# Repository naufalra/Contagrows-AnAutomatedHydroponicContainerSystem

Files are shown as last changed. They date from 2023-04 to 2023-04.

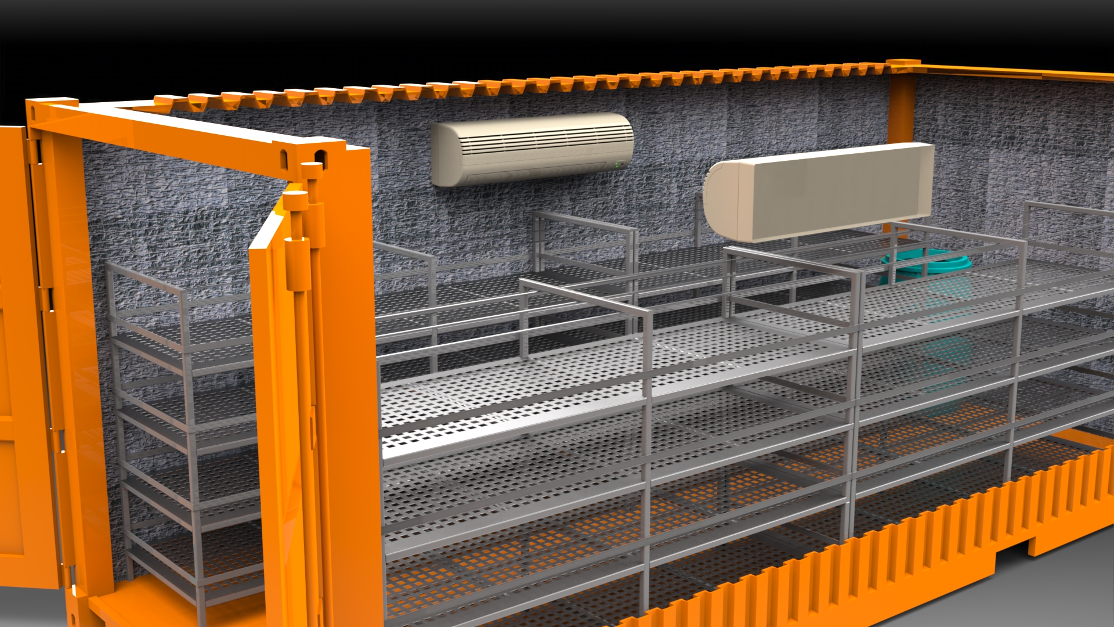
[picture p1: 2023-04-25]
3. Mechanical/render 2.jpg

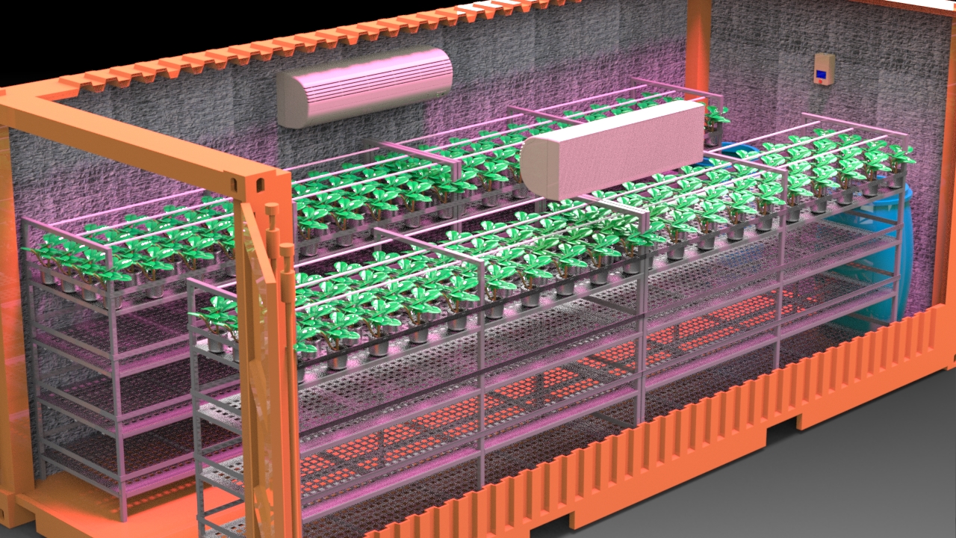
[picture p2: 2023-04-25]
3. Mechanical/Contagrov 3.jpg

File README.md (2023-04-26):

# Contagrows - An Automated Hydroponic Container System
# Project Overview

Container farms are becoming increasingly popular within the controlled environment agriculture industry. These farms are usually vertical farming systems installed inside a shipping container. The main objective is to make sure the local temperature is below 16 degrees Celcius with 80% of humidity so the plant can grow inside a controlled hygiene container. To do so, the container is equipped with AC, Fans, and an automatic watering and monitoring system.



During the manufacturing process, we had a lot of discussions with good friends from agricultural technology and PIAT (Center for Agro-Technology Innovation) UGM to produce a suitable and sustainable product.

Among our discussion topics was the system's design to meet the plant and electronic requirements. The discussion process resulted in the flow chart below



# Directory

To short things out, this is the directories of this project.

- [Article](https://www.linkedin.com/posts/naufalaryaputra_contagrow-an-automated-container-hydroponic-activity-6986608747372494849-8hf9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)
 - [Electrical Design](https://github.com/naufalra/Contagrows/tree/main/1.%20Electrical)
 - [Mechanical Design](https://github.com/naufalra/Contagrows/tree/main/3.%20Mechanical)
 - [Arduino Program](https://github.com/naufalra/Contagrows/tree/main/2.%20Firmware)

# Intelligent property rights

**Alat Otomasi dan Monitoring Budidaya Hidroponik**

```bash
  https://pdki-indonesia.dgip.go.id/detail/A00202203526?type=di&keyword=A00202203526 
```

**Media Tanam Pertanian Vertikal Hidroponik pada Kontainer**

```bash
 https://pdki-indonesia.dgip.go.id/detail/A00202203525?type=di&keyword=A00202203525
```

# Final Result
Electrical

## Electronics System
The control system itself is using Arduino Mega2560 as the main processor. The Arduino is connected to several built in sensors like DHT11, BME280, the boards is also provide more ports for additional sensor.
Electrical

## Wiring
We divided the panel into two parts to simplify the troubleshooting process and panel tidiness. 

The right panel (the one without LCD) functions as an electrical panel directly connected to the source. This panel also acts as the main switch.

The second panel only serves as the system control and automation of the tool. All control, monitoring, and automation are done through this panel. It is on this panel that the Arduino and sensors are placed.
Electrical

Electrical

We realize that many things can be improved in our electronic and wiring systems, but we have not had the chance to do so due to limited time. The safety process has also not been maximized because all energy has been diverted to the automation system.

## Mechanical Design
This system utilizes a 20-foot container to work. The container was chosen because it is easier to place in urban areas. Still, on the inside, we added several other components to support the needs, including plant shelves, setting panels, and screen protectors on boards to protect from water and dust.

### Shelf
The shelf is designed to accommodate approximately 1000 plant seeds placed in polybags. The rack design considers the plant seeds' maximum capacity and the container's space.

Shelfs

### Panel Box
The panel box is used as the setting center of the tool before the automation process takes place. In addition, on the panel, there is also a sensor reading value viewer to be monitored.

PanelBox

### LCD protectors
We also ad LCD protector as an additional protection for LCD from dust and water drops.
PanelBox

## Overall System
This is the final result of recent design
PanelBox

PanelBox

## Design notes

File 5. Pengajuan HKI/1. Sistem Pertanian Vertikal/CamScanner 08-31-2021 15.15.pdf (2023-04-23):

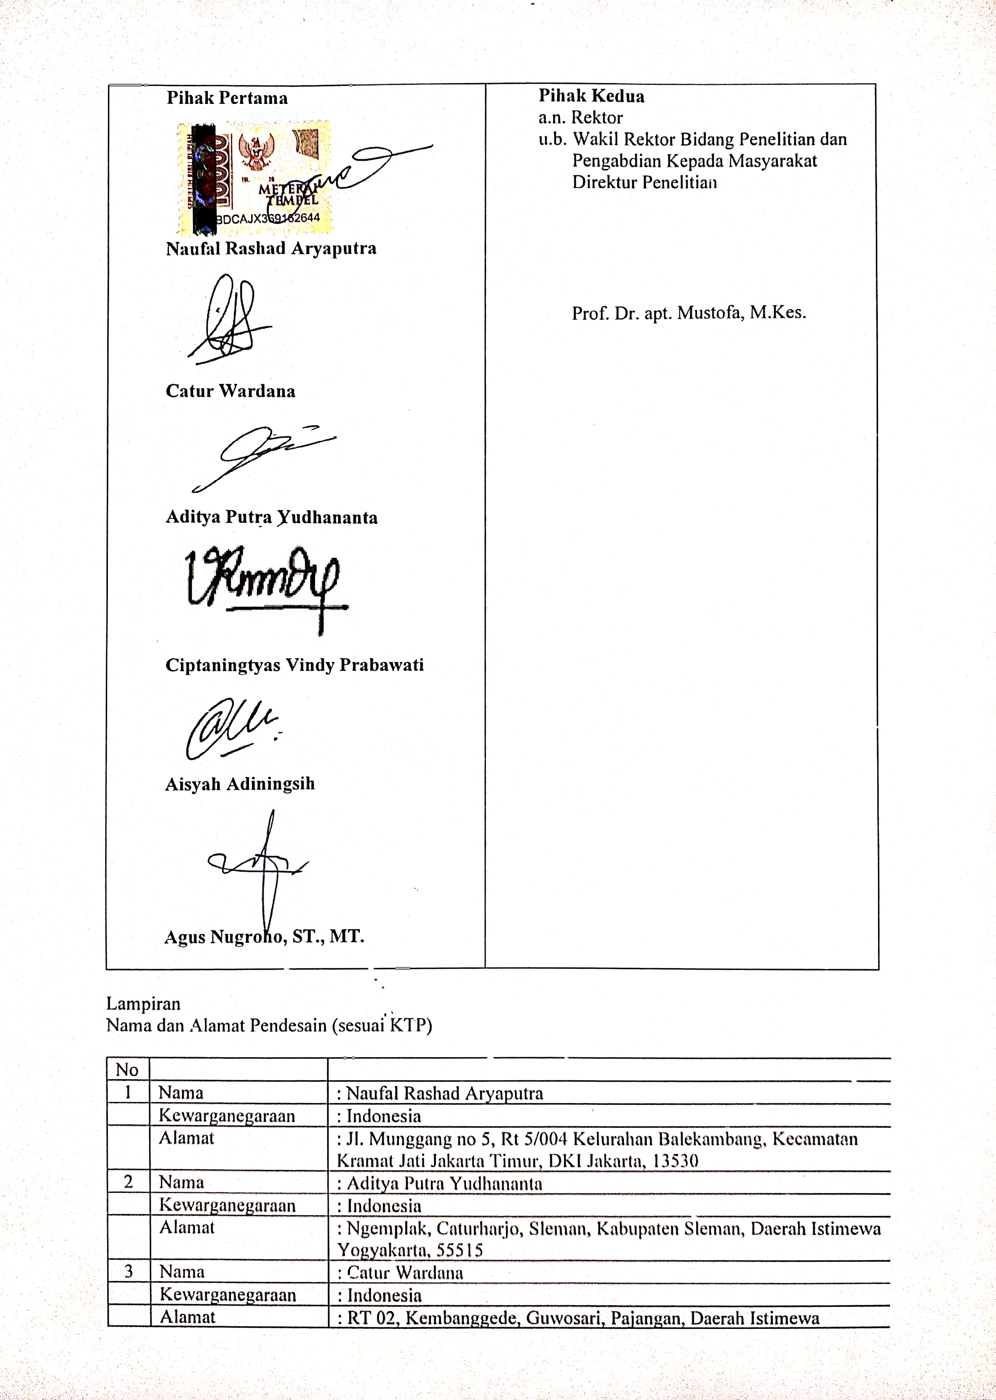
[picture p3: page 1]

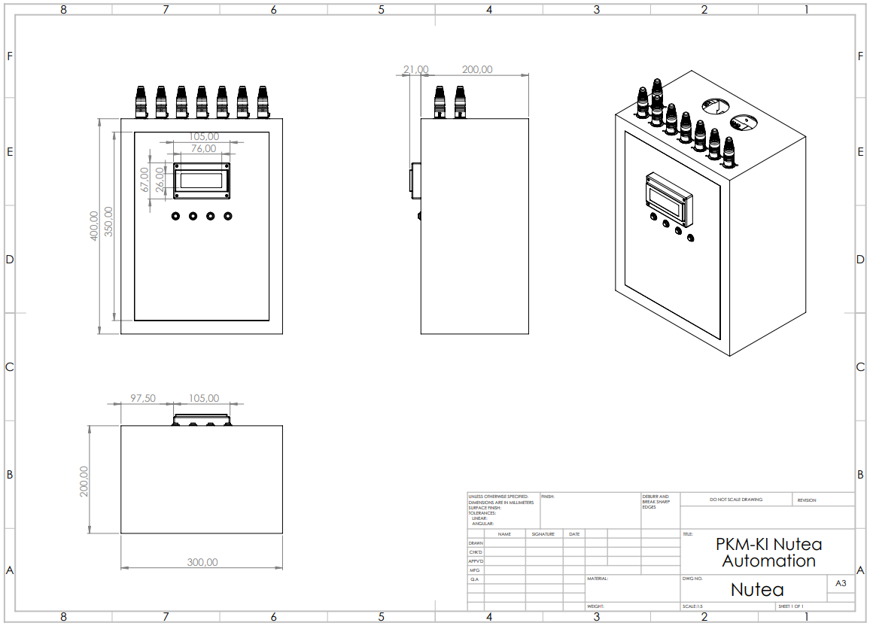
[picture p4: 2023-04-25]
3. Mechanical/Panel.png

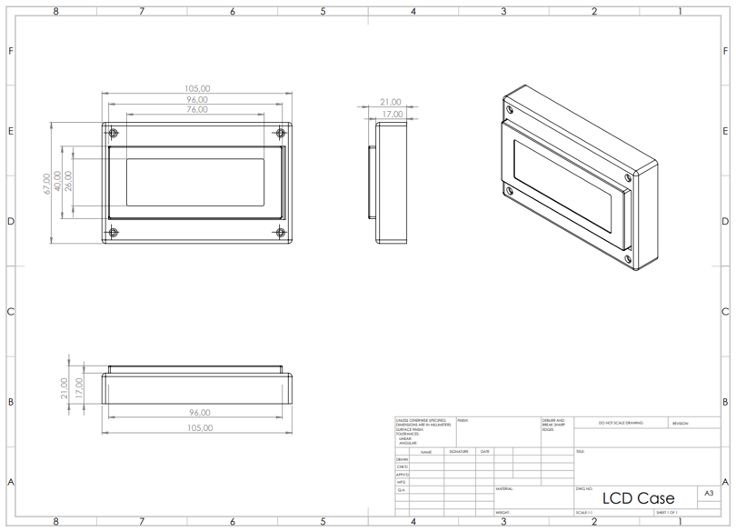
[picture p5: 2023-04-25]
3. Mechanical/LCD.png

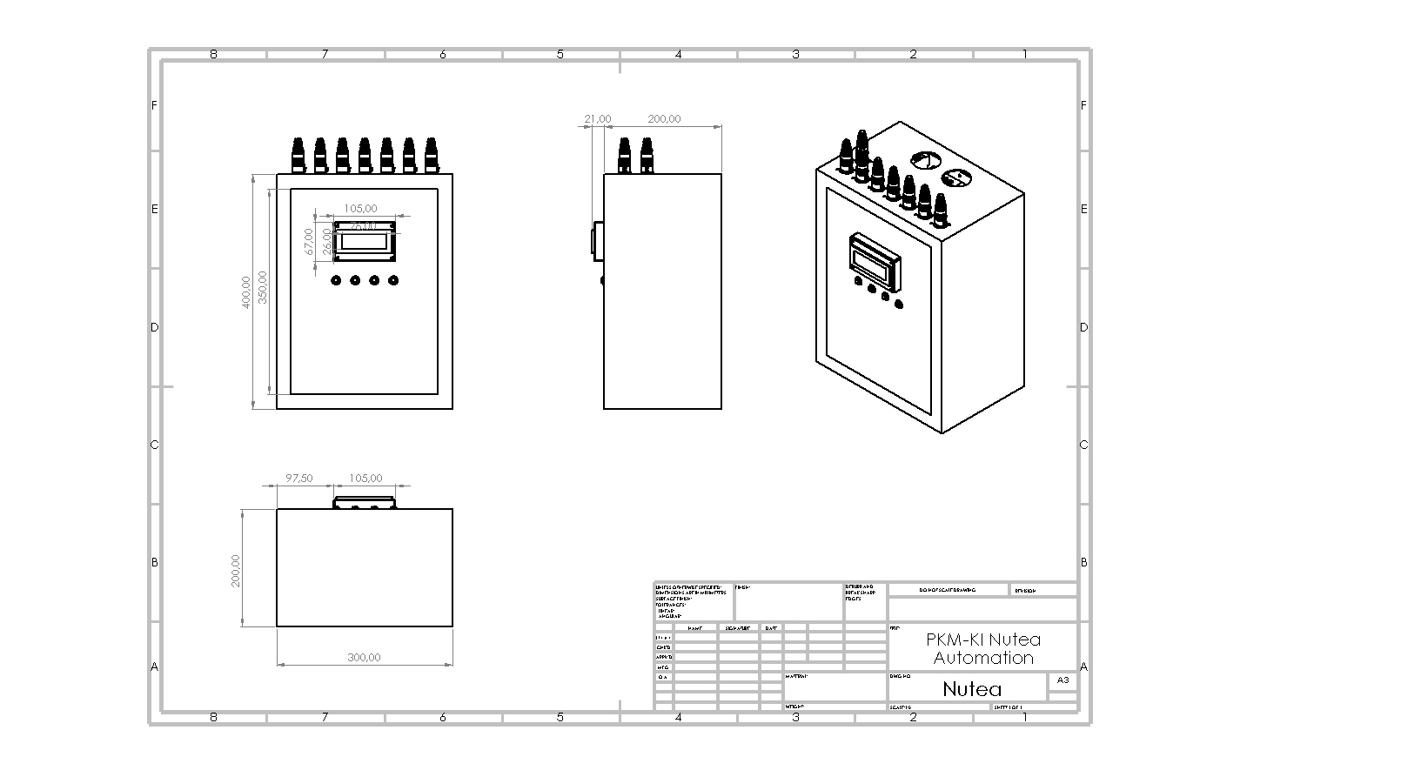
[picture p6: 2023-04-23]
3. Mechanical/Kotak Panel/Kotak Panel.JPG

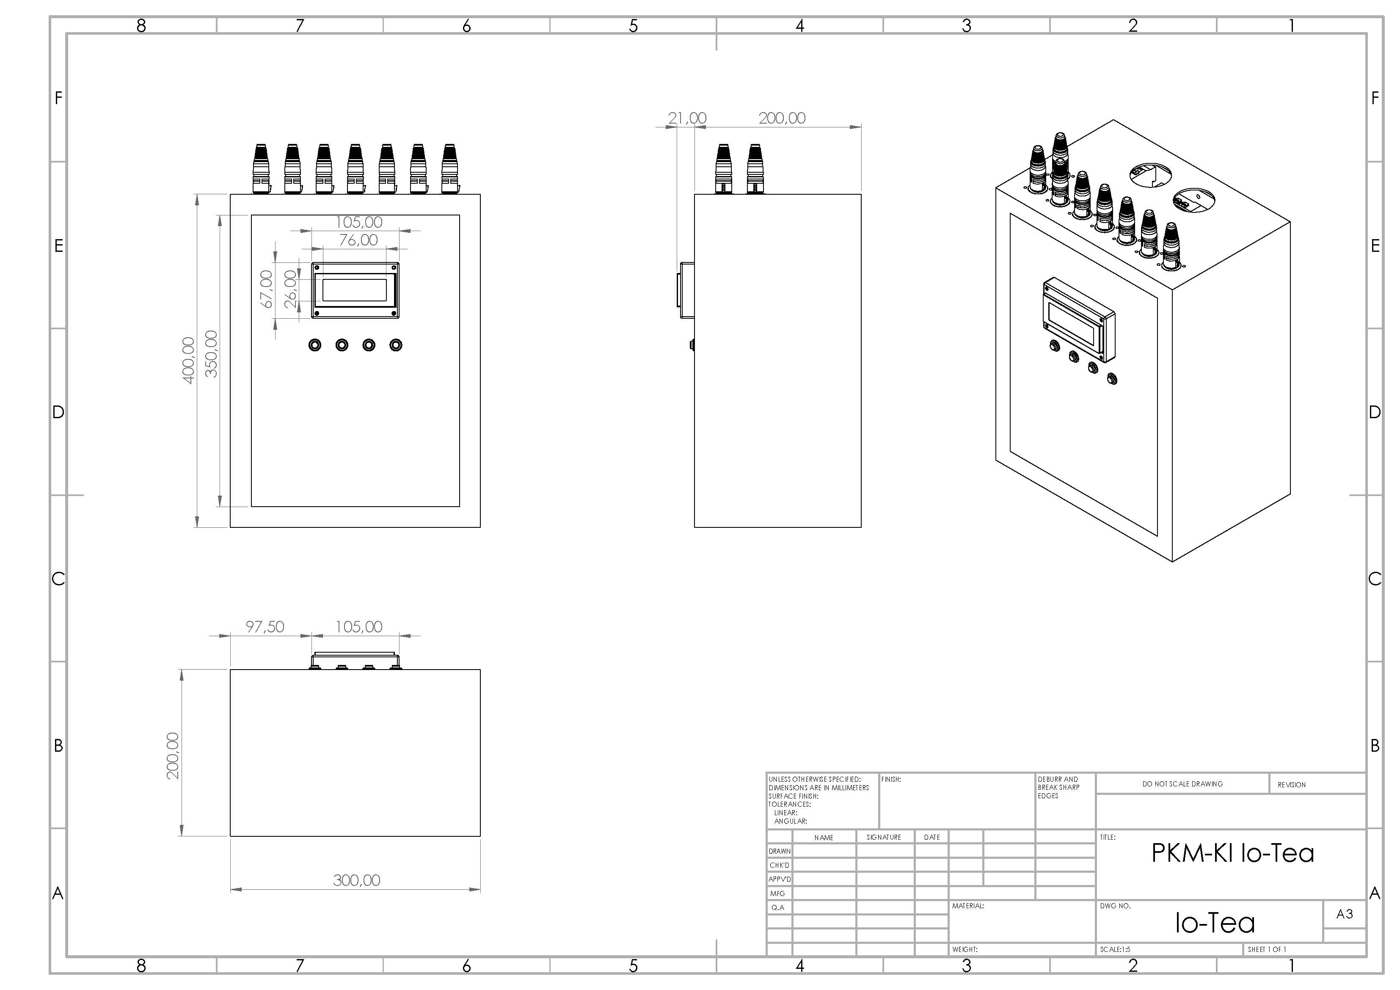
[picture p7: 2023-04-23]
3. Mechanical/Kotak Panel/LALALALLA.jpg

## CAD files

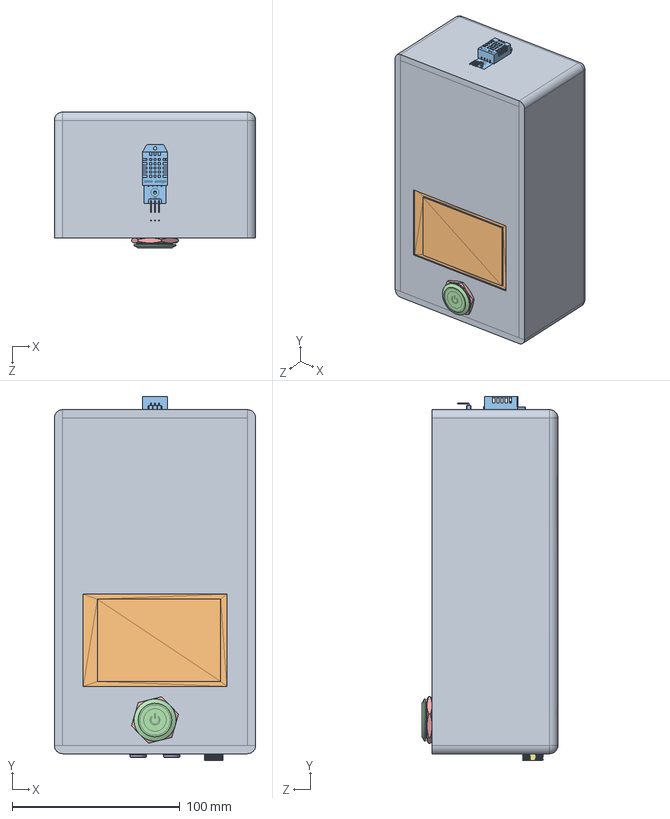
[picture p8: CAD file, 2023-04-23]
3. Mechanical/Shipping Container Assembly/Box.SLDASM
120.0 x 216.8 x 81.0 mm
NX4832T035
DHT22
22mm按钮
22mm金属按钮螺母
Amphenol RF 122440.step x 2
DC jack external.step

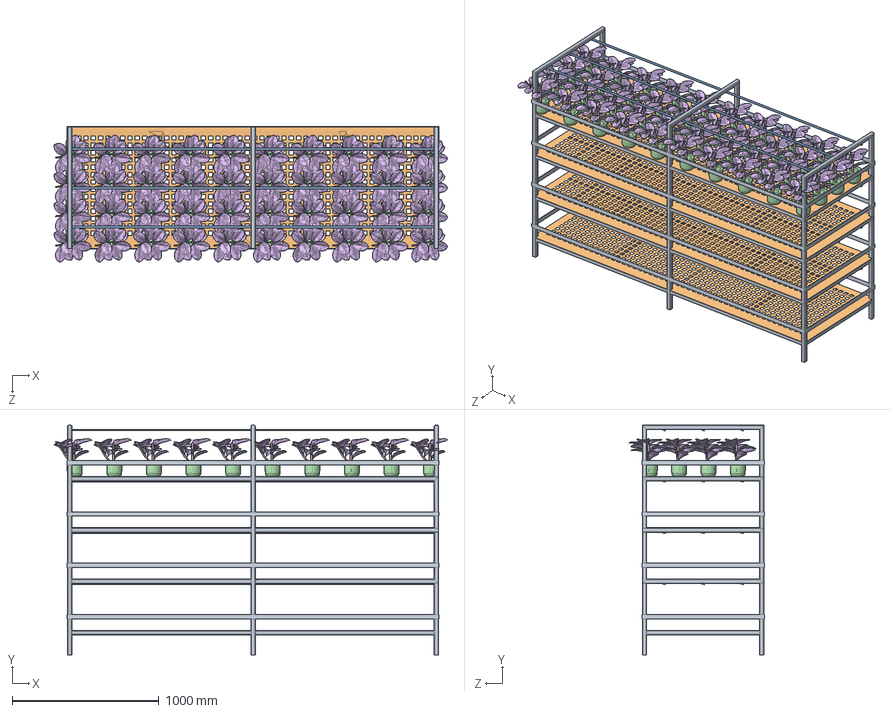
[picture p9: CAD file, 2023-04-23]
3. Mechanical/Shipping Container Assembly/Rak Assy Independ.SLDASM
2686.7 x 1565.0 x 926.4 mm
rak 1
plat x 4
LED SLOT x 4
B23-Vazo x 40
B23-Dal 1 x 40
B23-Yaprak 1 x 400

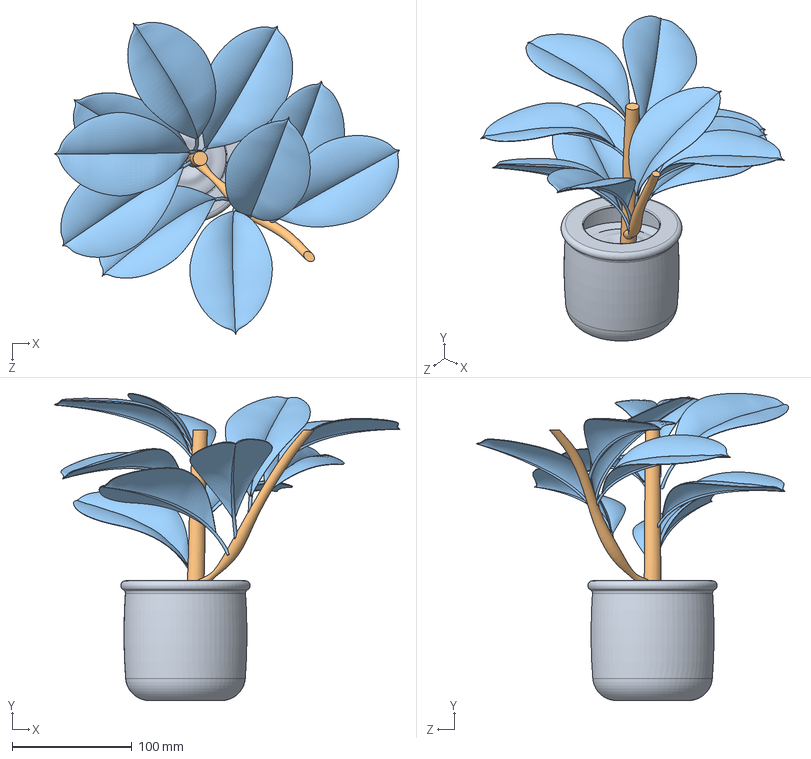
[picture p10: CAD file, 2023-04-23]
3. Mechanical/Shipping Container Assembly/B23-Montaj.SLDASM
288.7 x 256.3 x 260.6 mm
B23-Vazo
B23-Dal 1
B23-Yaprak 1 x 10

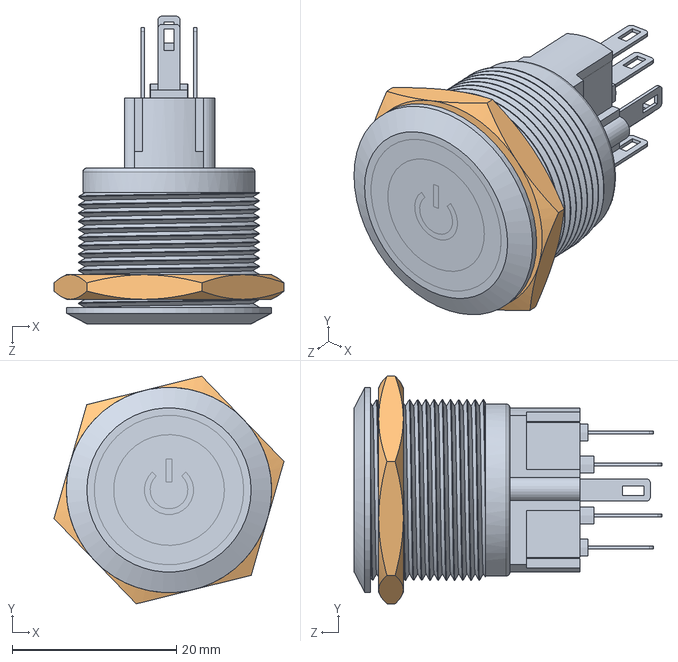
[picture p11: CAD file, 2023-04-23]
3. Mechanical/Shipping Container Assembly/22mm不锈钢按钮.SLDASM
28.0 x 27.7 x 37.5 mm
22mm按钮
22mm金属按钮螺母

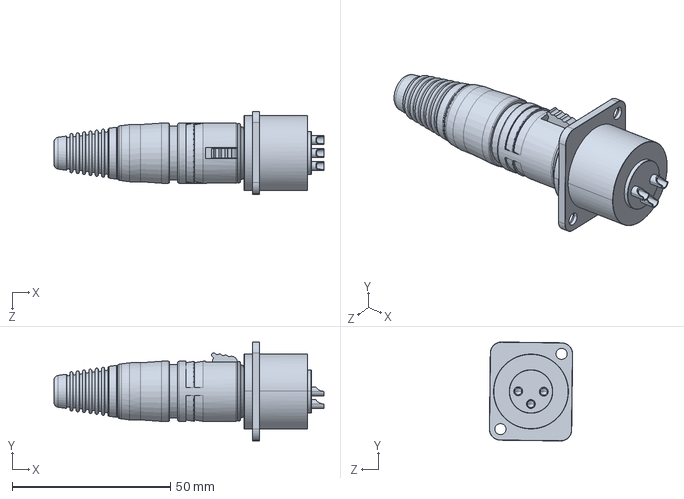
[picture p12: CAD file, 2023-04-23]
3. Mechanical/Kotak Panel/Assem2.SLDPRT
85.2 x 31.2 x 26.3 mm

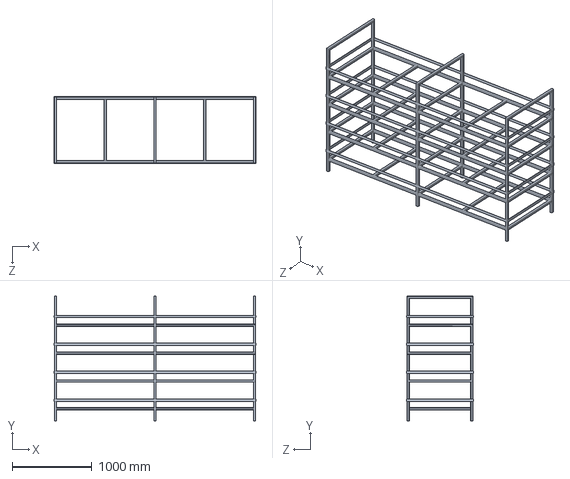
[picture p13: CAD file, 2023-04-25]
3. Mechanical/Rak/Rak_Contagrow.SLDPRT
2538.0 x 1565.0 x 836.0 mm

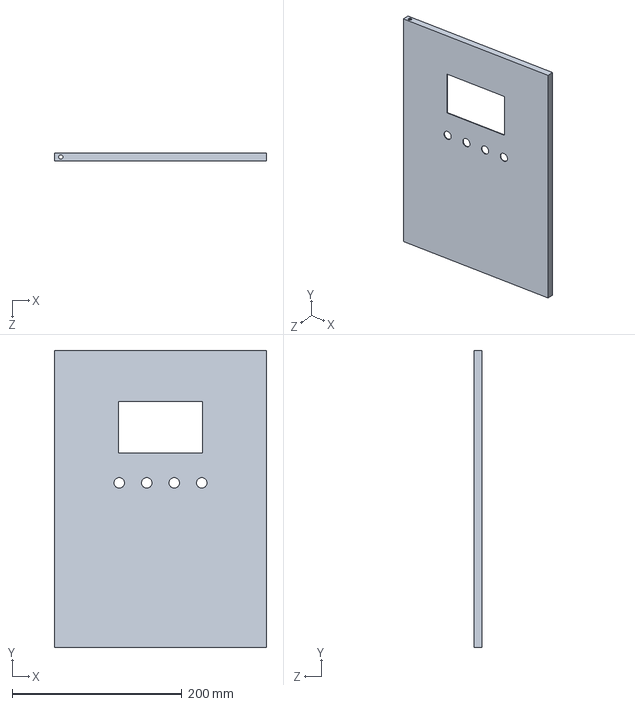
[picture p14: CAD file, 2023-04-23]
3. Mechanical/Kotak Panel/Kotak Panel_2.SLDPRT
250.0 x 350.0 x 10.0 mm

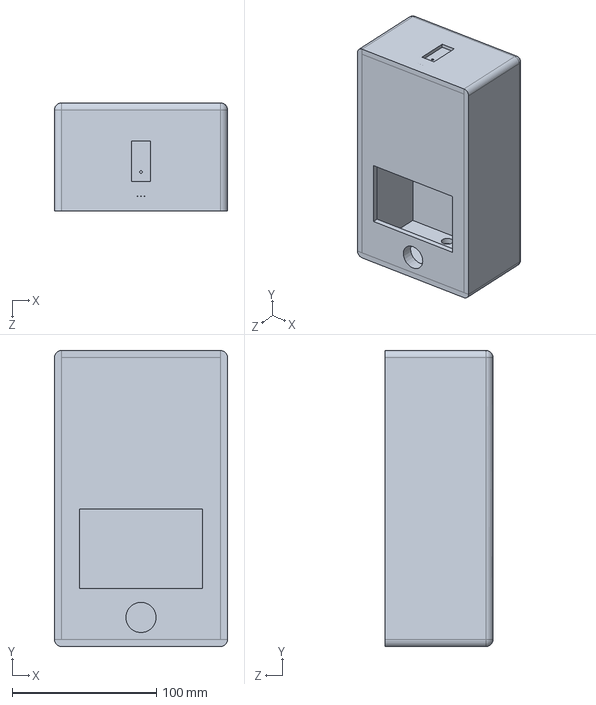
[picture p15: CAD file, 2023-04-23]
3. Mechanical/Shipping Container Assembly/Part2.SLDPRT
120.0 x 205.0 x 75.0 mm

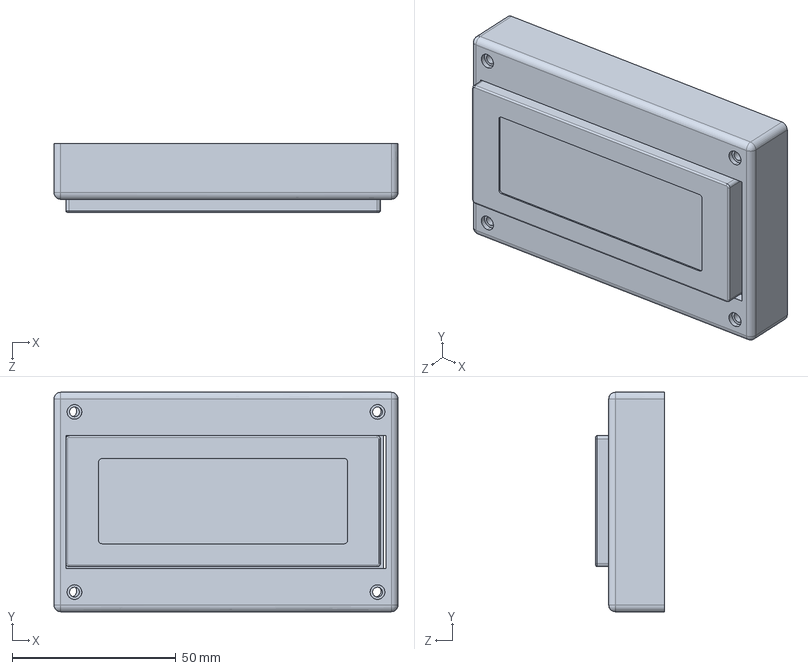
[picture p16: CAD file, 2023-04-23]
3. Mechanical/Kotak Panel/LCD.SLDPRT
105.0 x 67.0 x 21.0 mm

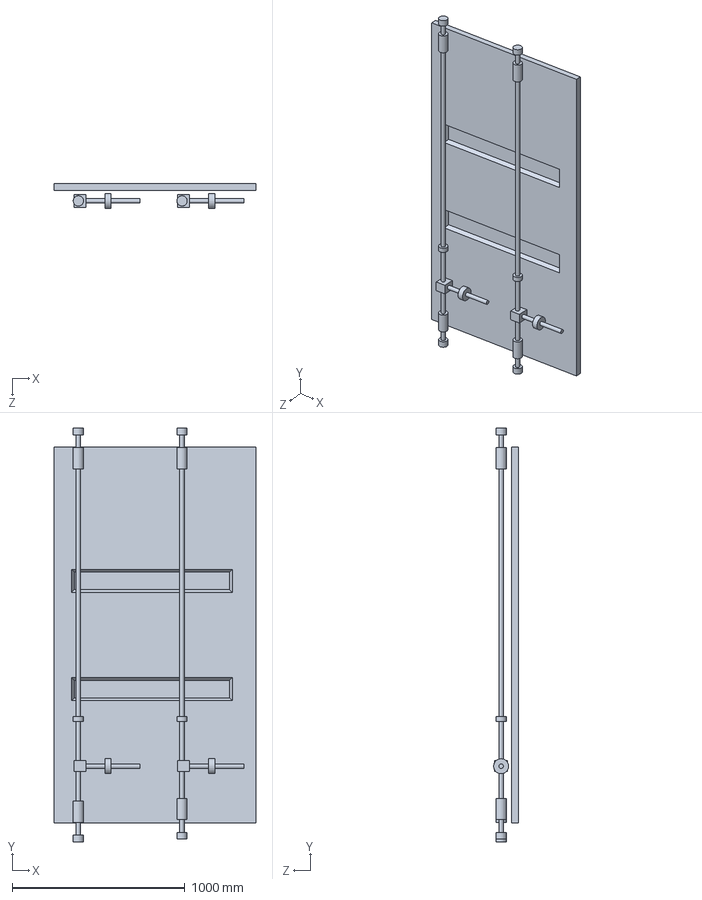
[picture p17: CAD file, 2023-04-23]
3. Mechanical/Shipping Container Assembly/Shipping container door.SLDPRT
1167.0 x 2396.0 x 143.5 mm

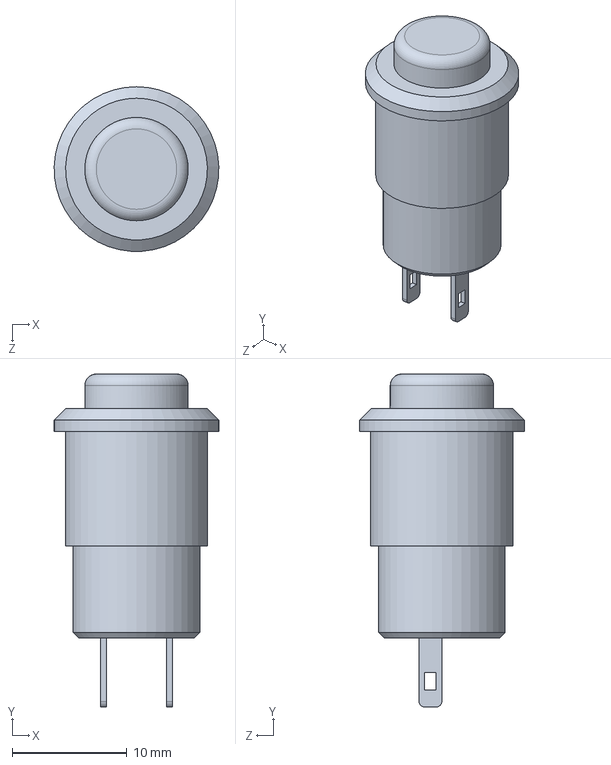
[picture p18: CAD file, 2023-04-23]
3. Mechanical/Kotak Panel/Push Button.SLDPRT
14.3 x 29.0 x 14.3 mm

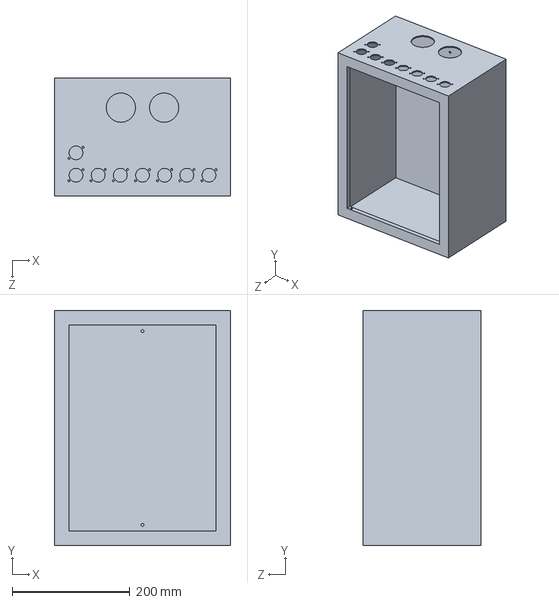
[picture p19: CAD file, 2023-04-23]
3. Mechanical/Kotak Panel/Kotak Panel_1.SLDPRT
300.0 x 400.0 x 200.0 mm

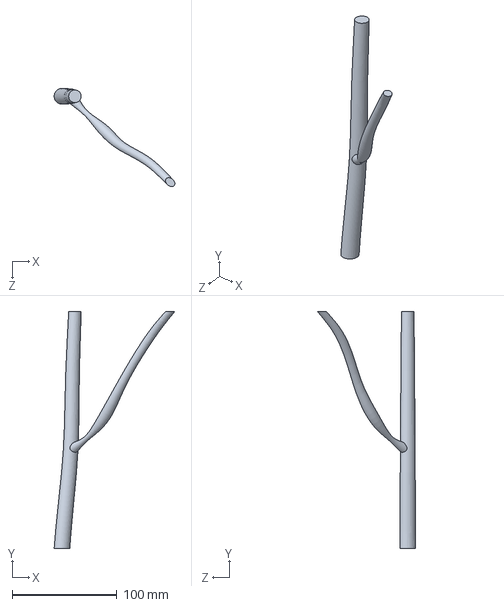
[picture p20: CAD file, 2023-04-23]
3. Mechanical/Shipping Container Assembly/B23-Dal 1.SLDPRT
115.0 x 225.9 x 93.6 mm

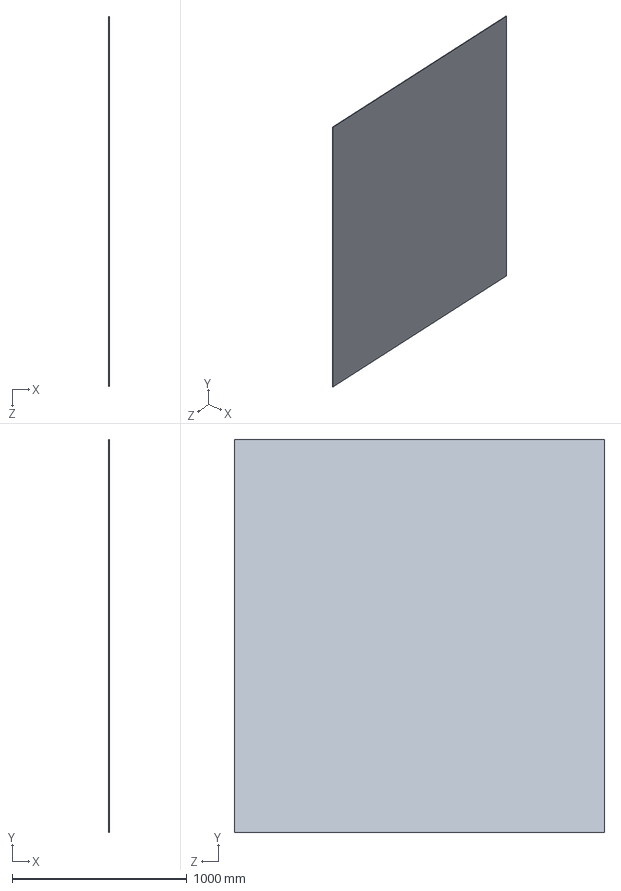
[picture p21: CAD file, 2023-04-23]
3. Mechanical/Shipping Container Assembly/aluminium belakang.SLDPRT
5.00 x 2247.0 x 2116.0 mm

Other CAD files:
3. Mechanical/Shipping Container Assembly/Shipping container left door.SLDPRT
3. Mechanical/Shipping Container Assembly/22mm按钮.SLDPRT
3. Mechanical/Shipping Container Assembly/Hinge.SLDPRT
3. Mechanical/Shipping Container Assembly/rak 1.SLDPRT
3. Mechanical/Kotak Panel/Kotak Panel gambar 3.SLDDRW
3. Mechanical/Kotak Panel/Kotak Panel.SLDDRW
3. Mechanical/Kotak Panel/Kotak Panel2.SLDDRW
3. Mechanical/Kotak Panel/LCD.SLDDRW
3. Mechanical/Rak/Rak_Contagrow.SLDDRW
3. Mechanical/Shipping Container Assembly/22mm金属按钮螺母.SLDPRT
3. Mechanical/Shipping Container Assembly/B23-Vazo.SLDPRT
3. Mechanical/Shipping Container Assembly/B23-Yaprak 1.SLDPRT
3. Mechanical/Shipping Container Assembly/DHT22.SLDPRT
3. Mechanical/Shipping Container Assembly/LED SLOT.SLDPRT
3. Mechanical/Shipping Container Assembly/Left Hinge.SLDPRT
3. Mechanical/Shipping Container Assembly/NX4832T035.SLDPRT
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

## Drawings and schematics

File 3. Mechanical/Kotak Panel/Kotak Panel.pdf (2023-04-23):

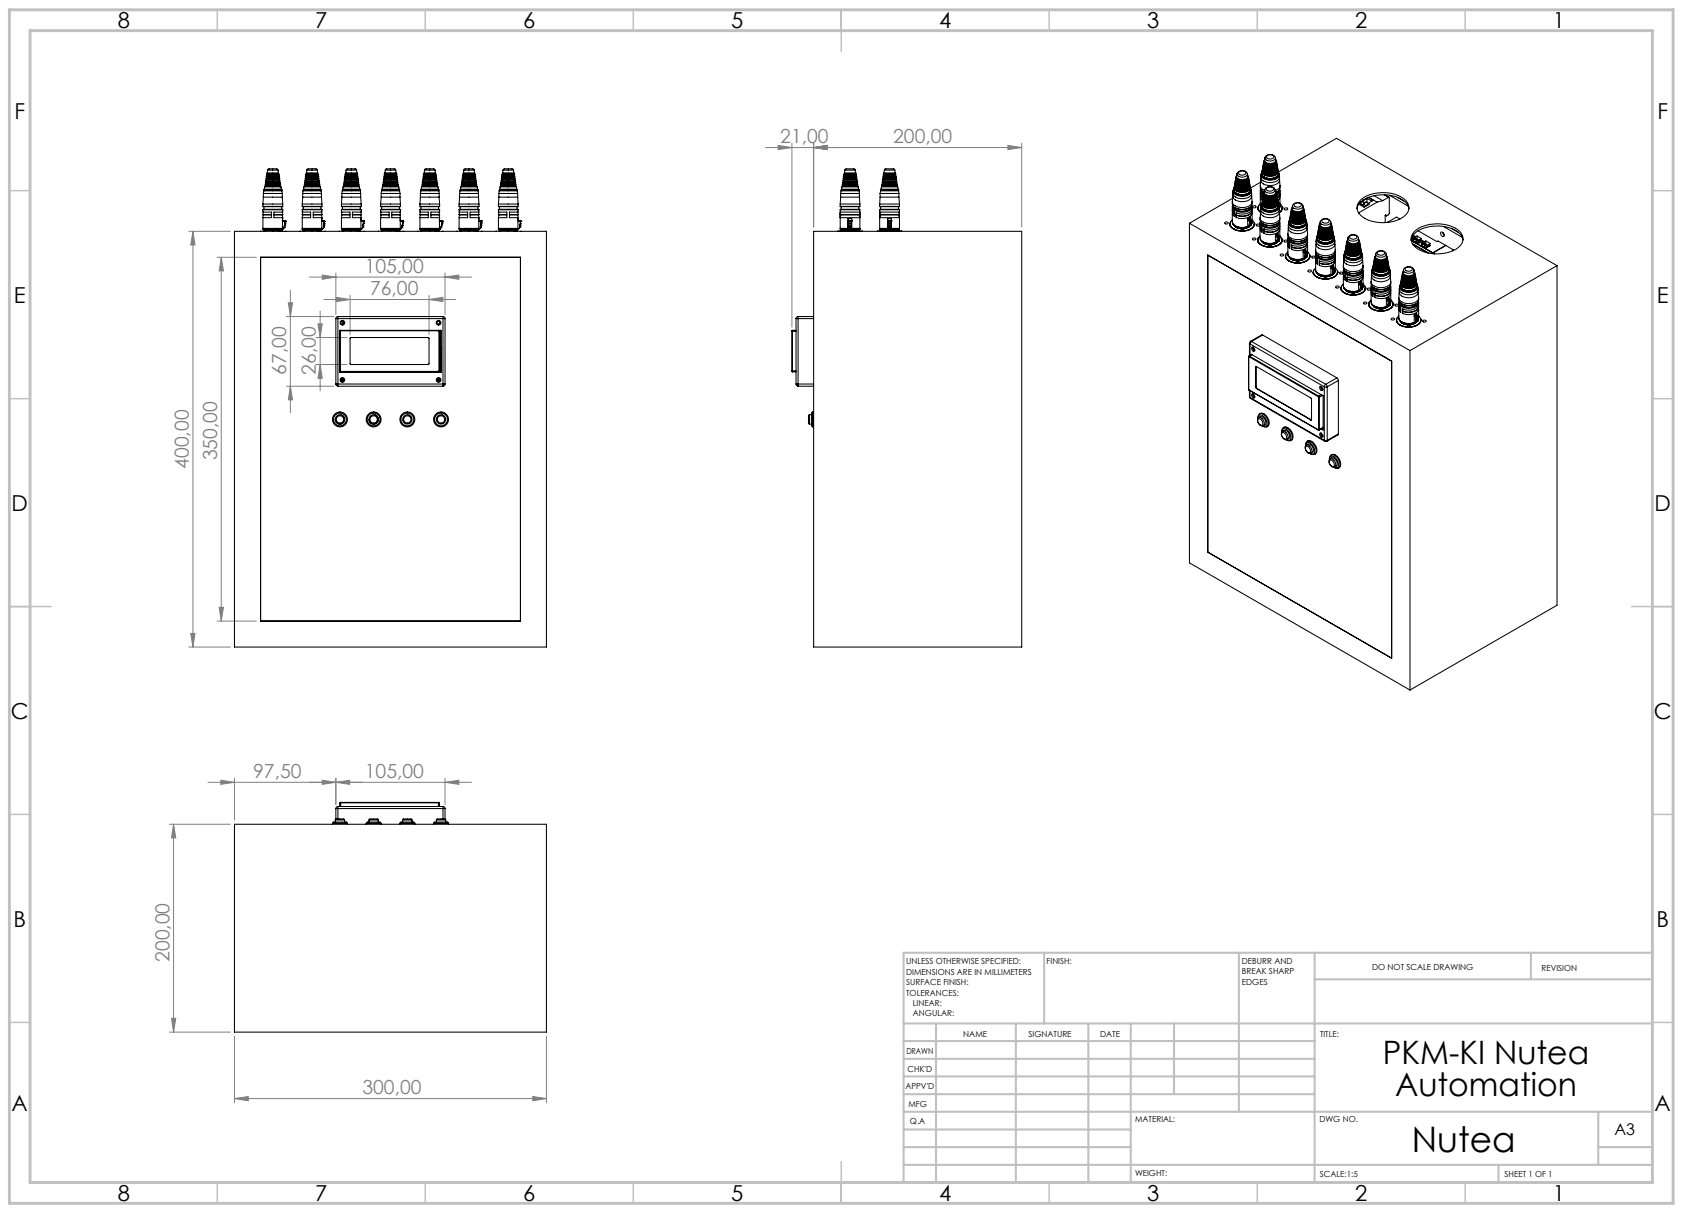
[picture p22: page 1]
FINISH:; DEBURR AND; BREAK SHARP; DO NOT SCALE DRAWING; REVISION; SCALE:1:5; SHEET 1 OF 1

UNLESS OTHERWISE SPECIFIED:
DIMENSIONS ARE IN MILLIMETERS
SURFACE FINISH:
TOLERANCES:
LINEAR:
ANGULAR:

NAME | SIGNATURE | DATE | | | | TITLE: PKM-KI Nutea Automation

DRAWN
CHK'D
APPV'D
MFG
Q.A | | | | MATERIAL: | DWG NO. Nutea | A3

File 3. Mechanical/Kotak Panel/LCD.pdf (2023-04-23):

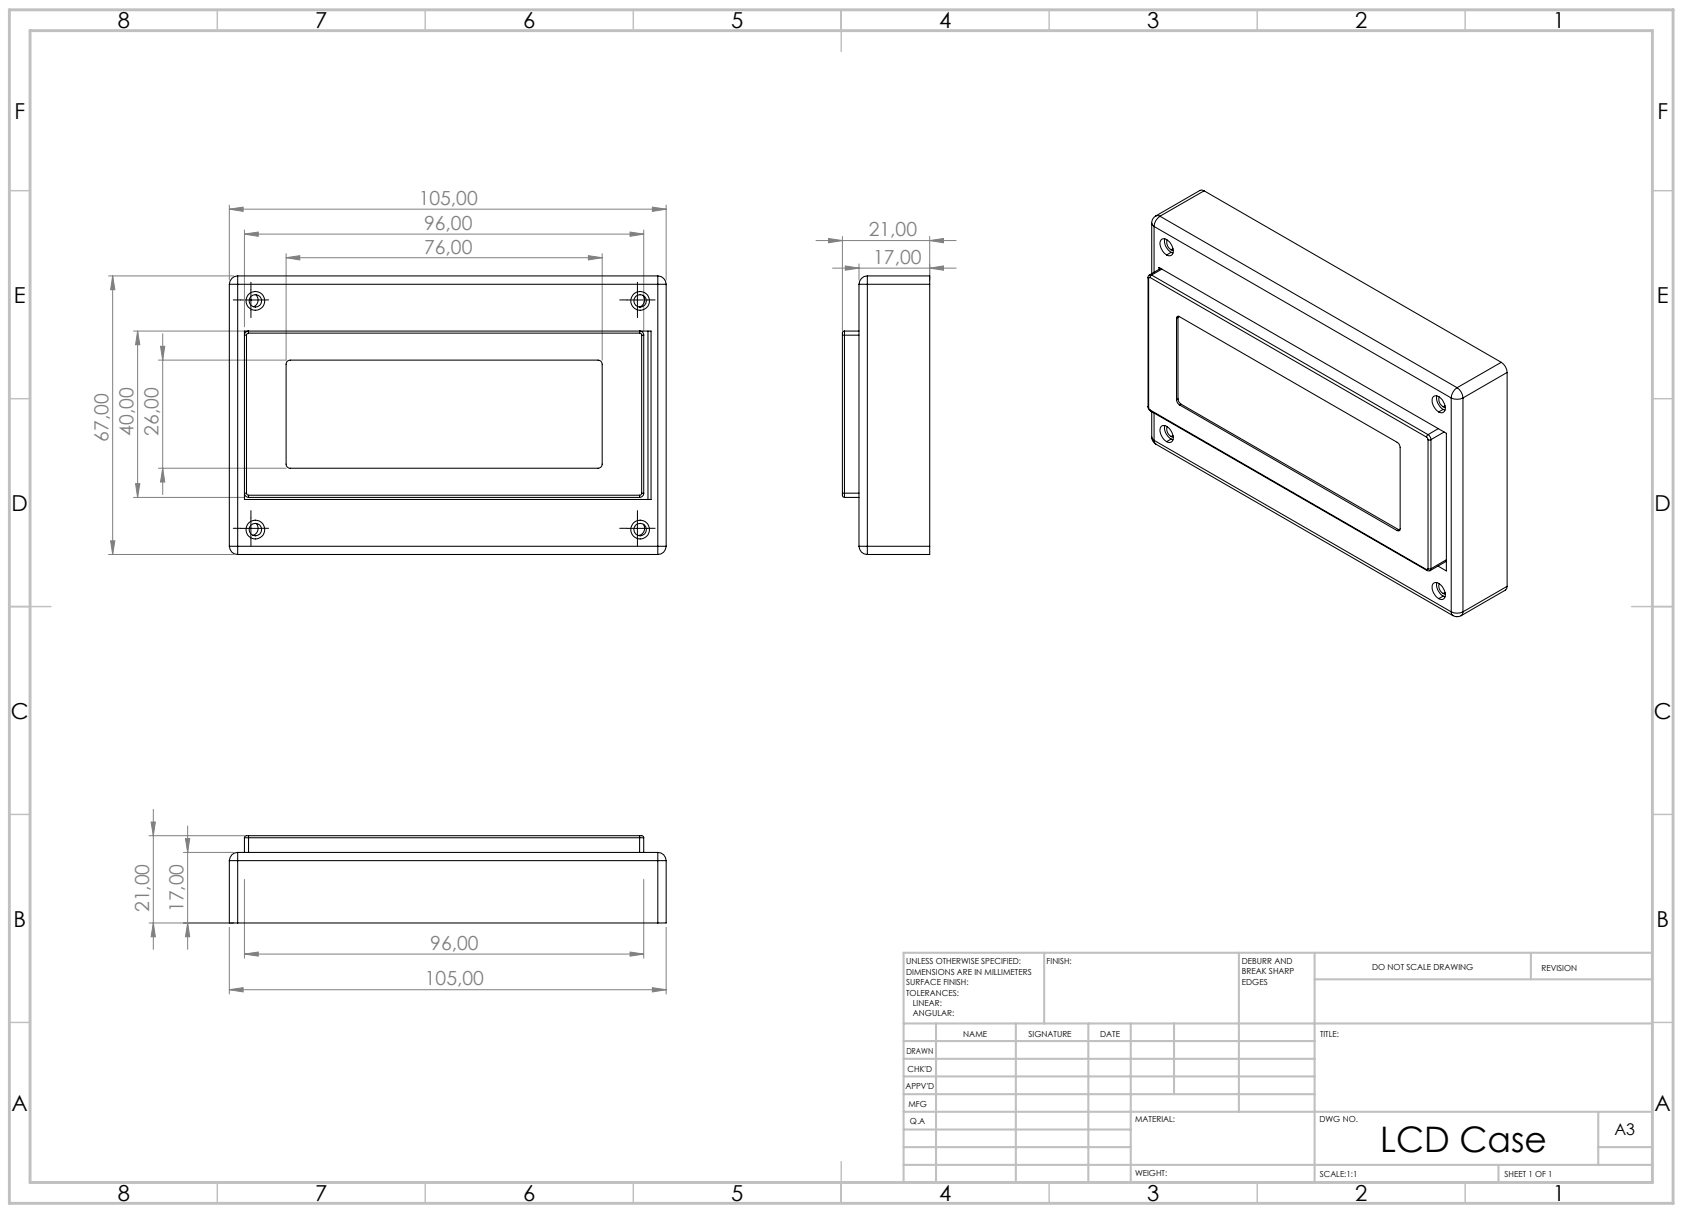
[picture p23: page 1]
FINISH:; DEBURR AND; BREAK SHARP; DO NOT SCALE DRAWING; REVISION; SCALE:1:1; SHEET 1 OF 1

UNLESS OTHERWISE SPECIFIED:
DIMENSIONS ARE IN MILLIMETERS
SURFACE FINISH:
TOLERANCES:
LINEAR:
ANGULAR:

NAME | SIGNATURE | DATE | | | | TITLE:

DRAWN
CHK'D
APPV'D
MFG
Q.A | | | | MATERIAL: | DWG NO. LCD Case | A3

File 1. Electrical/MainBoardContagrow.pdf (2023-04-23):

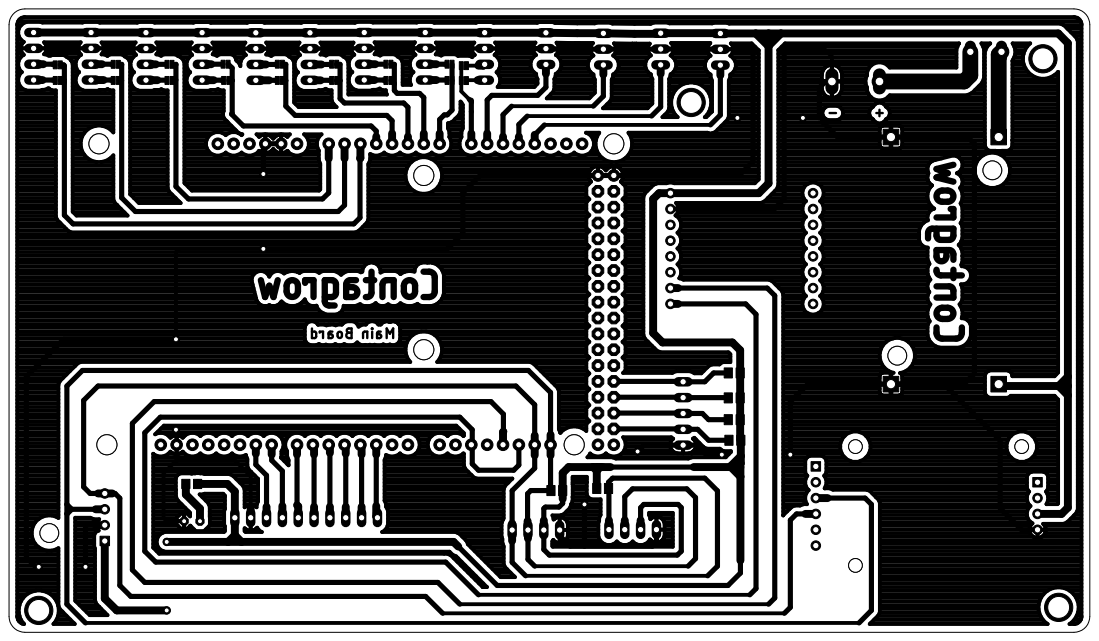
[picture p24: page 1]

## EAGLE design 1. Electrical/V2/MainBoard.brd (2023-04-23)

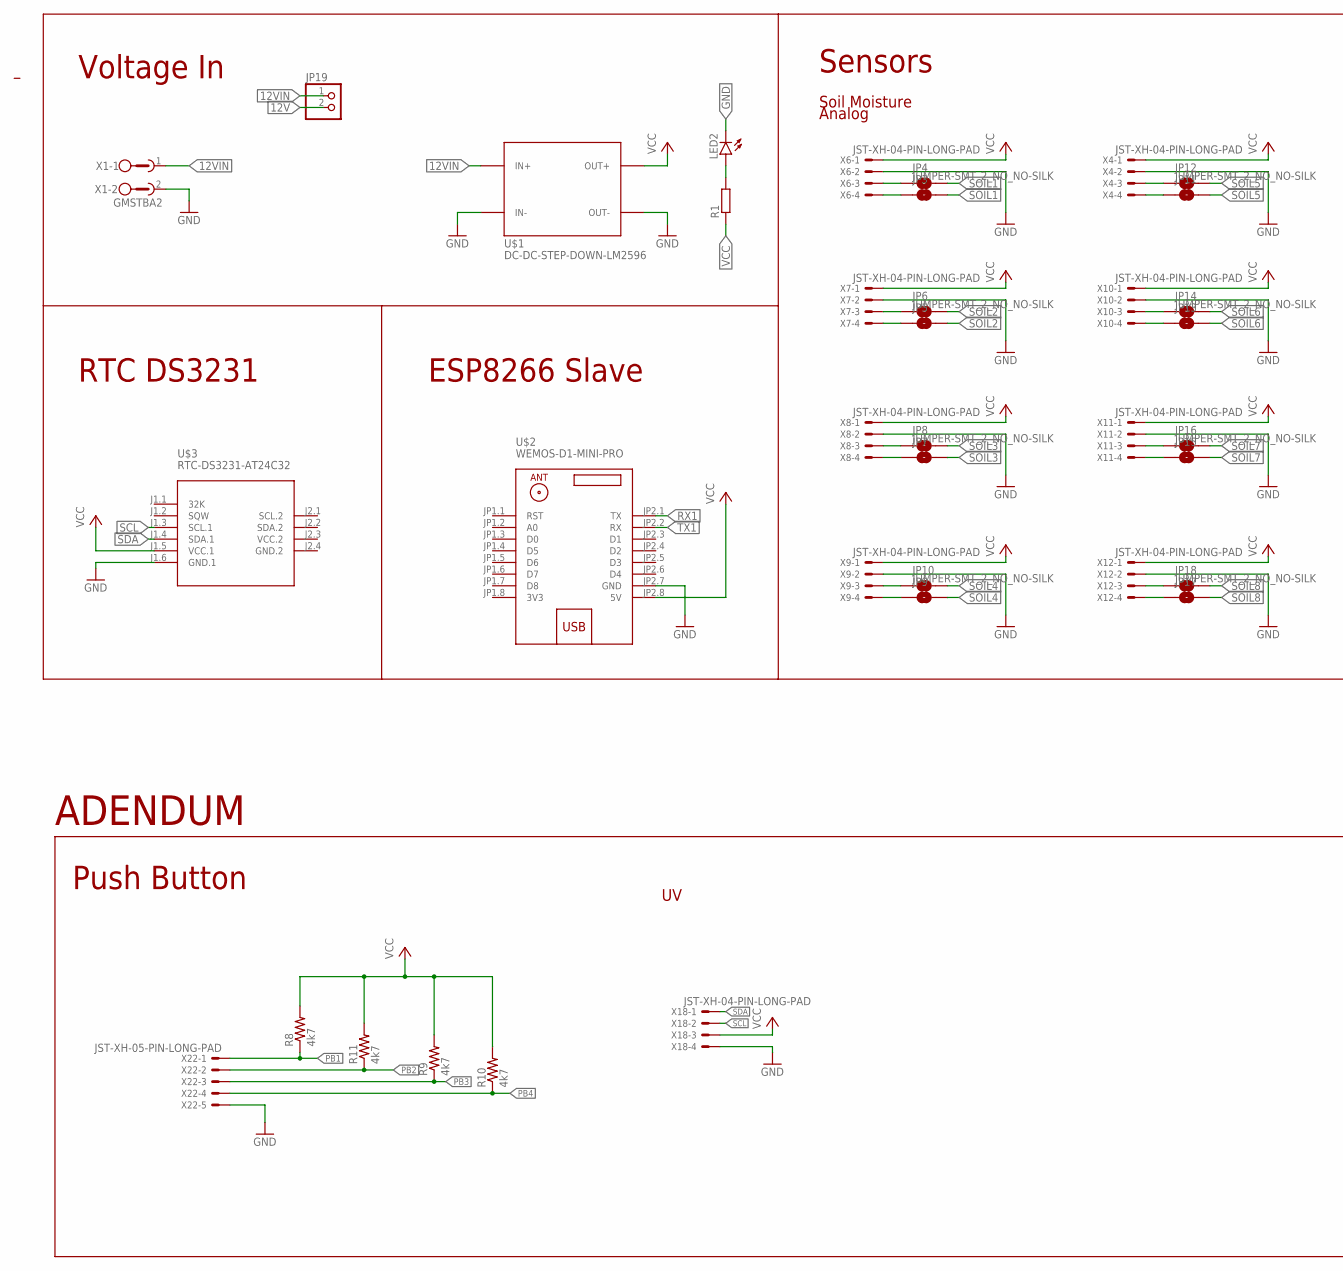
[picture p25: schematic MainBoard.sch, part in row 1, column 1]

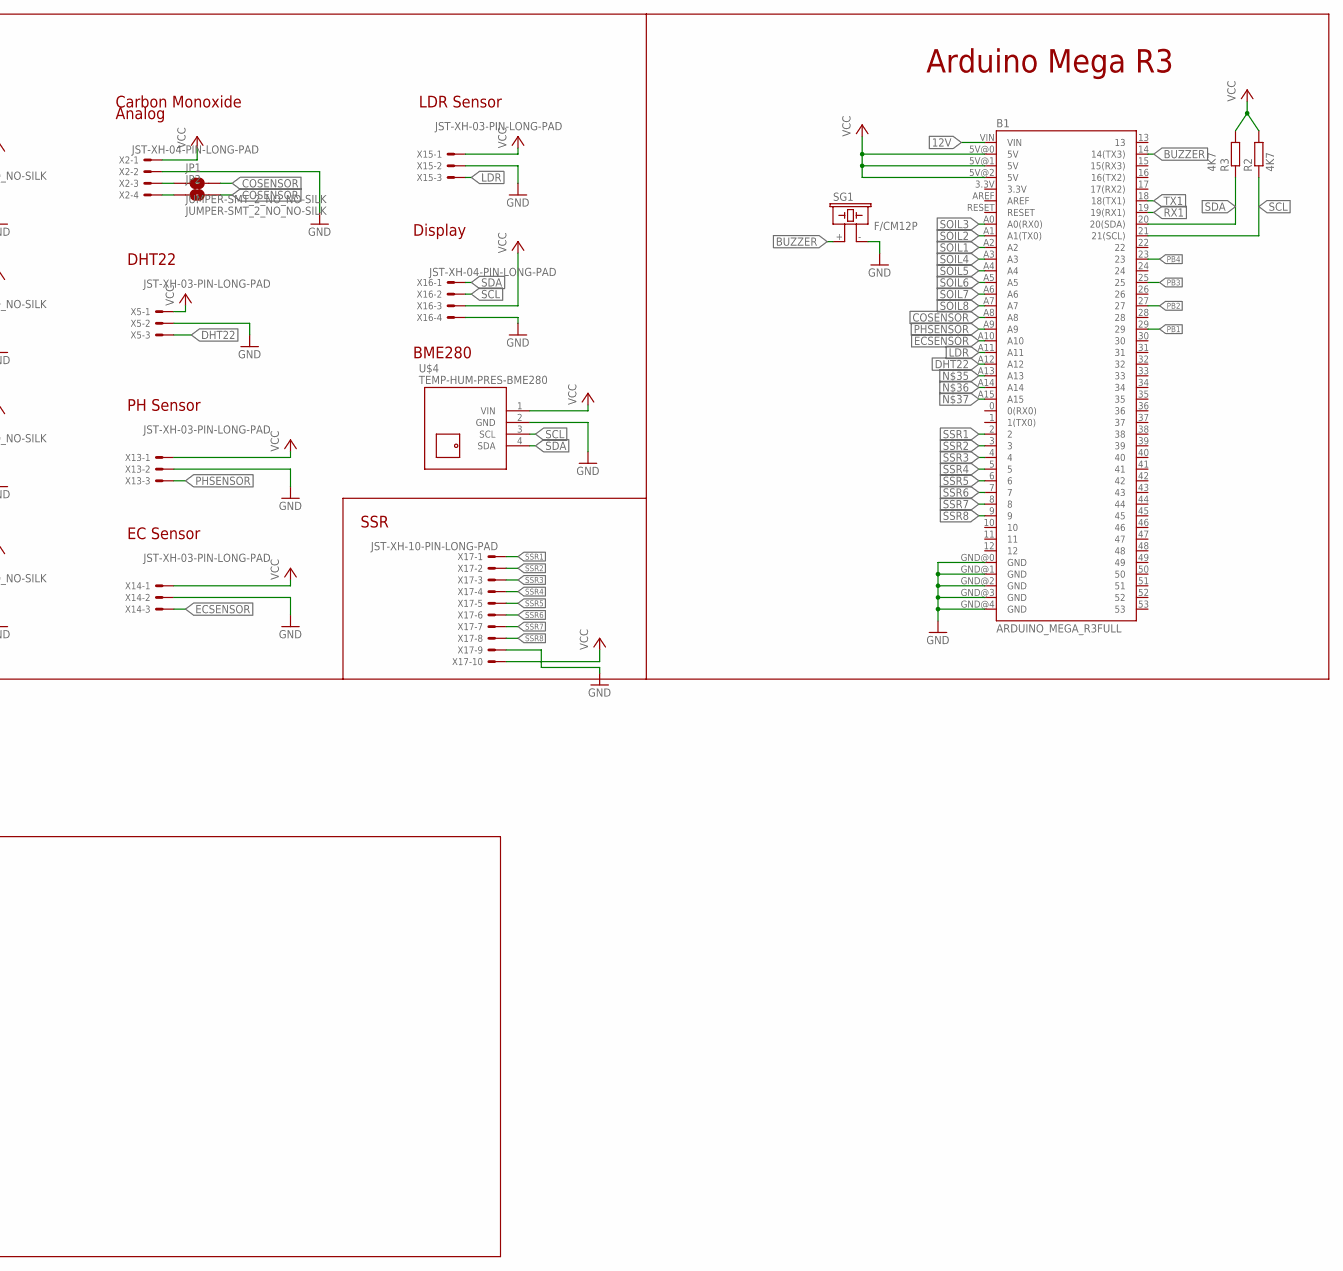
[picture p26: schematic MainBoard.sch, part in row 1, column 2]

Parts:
B1: ARDUINO_MEGA_R3FULL; ARDUINO_MEGA
JP1, JP2, JP3, JP4, JP5, JP6, JP7, JP8, JP9, JP10, JP11, JP12, JP13, JP14, JP15, JP16, JP17, JP18: JUMPER-SMT_2_NO_NO-SILK; SMT-JUMPER_2_NO_NO-SILK
JP19: PINHD-1X2; 1X02
LED2: LED5MM
R1: R-EU_R0805; R0805
R2, R3: 4K7; M0805
R8, R9, R10, R11: 4k7; M0805
SG1: F/CM12P
U$1: DC-DC-STEP-DOWN-LM2596
U$2: WEMOS-D1-MINI-PRO
U$3: RTC-DS3231-AT24C32
U$4: TEMP-HUM-PRES-BME280
X1: GMSTBA2
X2, X4, X6, X7, X8, X9, X10, X11, X12, X16, X18: JST-XH-04-PIN-LONG-PAD; JST-XH-04-PACKAGE-LONG-PAD
X5, X13, X14, X15: JST-XH-03-PIN-LONG-PAD; JST-XH-03-PACKAGE-LONG-PAD
X17: JST-XH-10-PIN-LONG-PAD; JST-XH-10-PACKAGE-LONG-PAD
X22: JST-XH-05-PIN-LONG-PAD; JST-XH-05-PACKAGE-LONG-PAD

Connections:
3V3: U$2.JP1.8 (3V3)
12V: B1.VIN, JP19.2
12VIN: JP19.1, U$1.IN+, X1.1
BUZZER: B1.14 (14(TX3)), SG1.+ (1)
COSENSOR: B1.A8, JP1.2, JP2.2
DHT22: B1.A12, X5.3
ECSENSOR: B1.A10, X14.3
GND: B1.GND@0 (GND), B1.GND@1 (GND), B1.GND@2 (GND), B1.GND@3 (GND), B1.GND@4 (GND), LED2.K (C), SG1.- (2), U$1.IN-, U$1.OUT-, U$2.JP2.7 (GND), U$3.J1.6 (GND.1), U$4.2 (GND), X1.2, X2.2, X4.2, X5.2, X6.2, X7.2, X8.2, X9.2, X10.2, X11.2, X12.2, X13.2, X14.2, X15.2, X16.4, X17.9, X18.4, X22.5
GND.2: U$3.J2.4 (GND.2)
LDR: B1.A11, X15.3
unnamed: JP1.1, X2.3
unnamed: JP2.1, X2.4
unnamed: JP3.1, X6.4
unnamed: JP4.1, X6.3
unnamed: LED2.A, R1.2
unnamed: JP5.1, X7.4
unnamed: JP6.1, X7.3
unnamed: JP7.1, X8.4
unnamed: JP8.1, X8.3
unnamed: JP9.1, X9.4
unnamed: JP10.1, X9.3
unnamed: JP11.1, X4.4
unnamed: JP12.1, X4.3
unnamed: JP13.1, X10.4
unnamed: JP14.1, X10.3
unnamed: JP15.1, X11.4
unnamed: JP16.1, X11.3
unnamed: JP17.1, X12.4
unnamed: JP18.1, X12.3
PB1: B1.29, R8.1, X22.1
PB2: B1.27, R11.1, X22.2
PB3: B1.25, R9.1, X22.3
PB4: B1.23, R10.1, X22.4
PHSENSOR: B1.A9, X13.3
RX1: B1.19 (19(RX1)), U$2.JP2.1 (TX)
SCL: B1.21 (21(SCL)), R2.1, U$3.J1.3 (SCL.1), U$4.3 (SCL), X16.2, X18.2
SDA: B1.20 (20(SDA)), R3.1, U$3.J1.4 (SDA.1), U$4.4 (SDA), X16.1, X18.1
SOIL1: B1.A2, JP3.2, JP4.2
SOIL2: B1.A1 (A1(TX0)), JP5.2, JP6.2
SOIL3: B1.A0 (A0(RX0)), JP7.2, JP8.2
SOIL4: B1.A3, JP9.2, JP10.2
SOIL5: B1.A4, JP11.2, JP12.2
SOIL6: B1.A5, JP13.2, JP14.2
SOIL7: B1.A6, JP15.2, JP16.2
SOIL8: B1.A7, JP17.2, JP18.2
SSR1: B1.2, X17.1
SSR2: B1.3, X17.2
SSR3: B1.4, X17.3
SSR4: B1.5, X17.4
SSR5: B1.6, X17.5
SSR6: B1.7, X17.6
SSR7: B1.8, X17.7
SSR8: B1.9, X17.8
TX1: B1.18 (18(TX1)), U$2.JP2.2 (RX)
VCC: B1.5V@0 (5V), B1.5V@1 (5V), B1.5V@2 (5V), R1.1, R2.2, R3.2, R8.2, R9.2, R10.2, R11.2, U$1.OUT+, U$2.JP2.8 (5V), U$3.J1.5 (VCC.1), U$4.1 (VIN), X2.1, X4.1, X5.1, X6.1, X7.1, X8.1, X9.1, X10.1, X11.1, X12.1, X13.1, X14.1, X15.1, X16.3, X17.10, X18.3
VCC.2: U$3.J2.3 (VCC.2)

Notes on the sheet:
Voltage In
Arduino Mega R3
RTC DS3231
ESP8266 Slave
Sensors
Carbon Monoxide
DHT22
Soil Moisture
PH Sensor
EC Sensor
Analog
LDR Sensor
Display
BME280
SSR
Push Button
ADENDUM

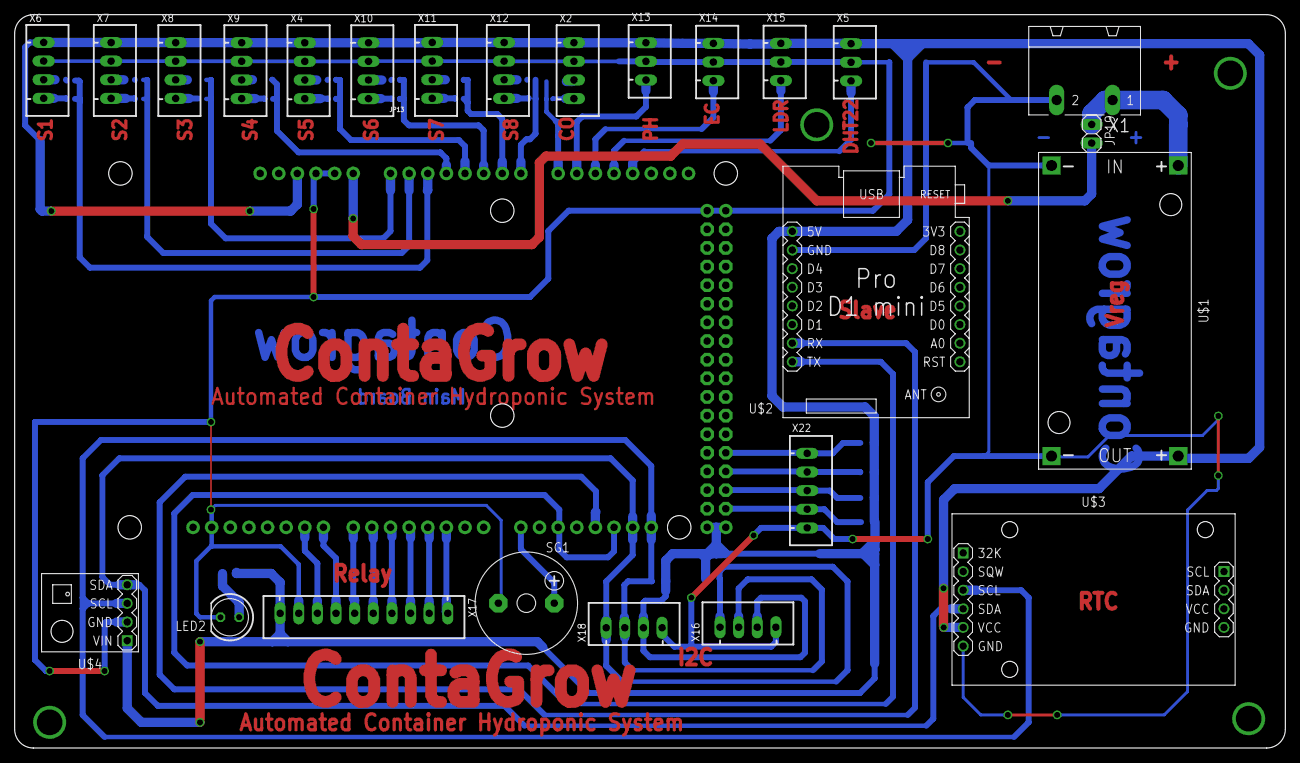
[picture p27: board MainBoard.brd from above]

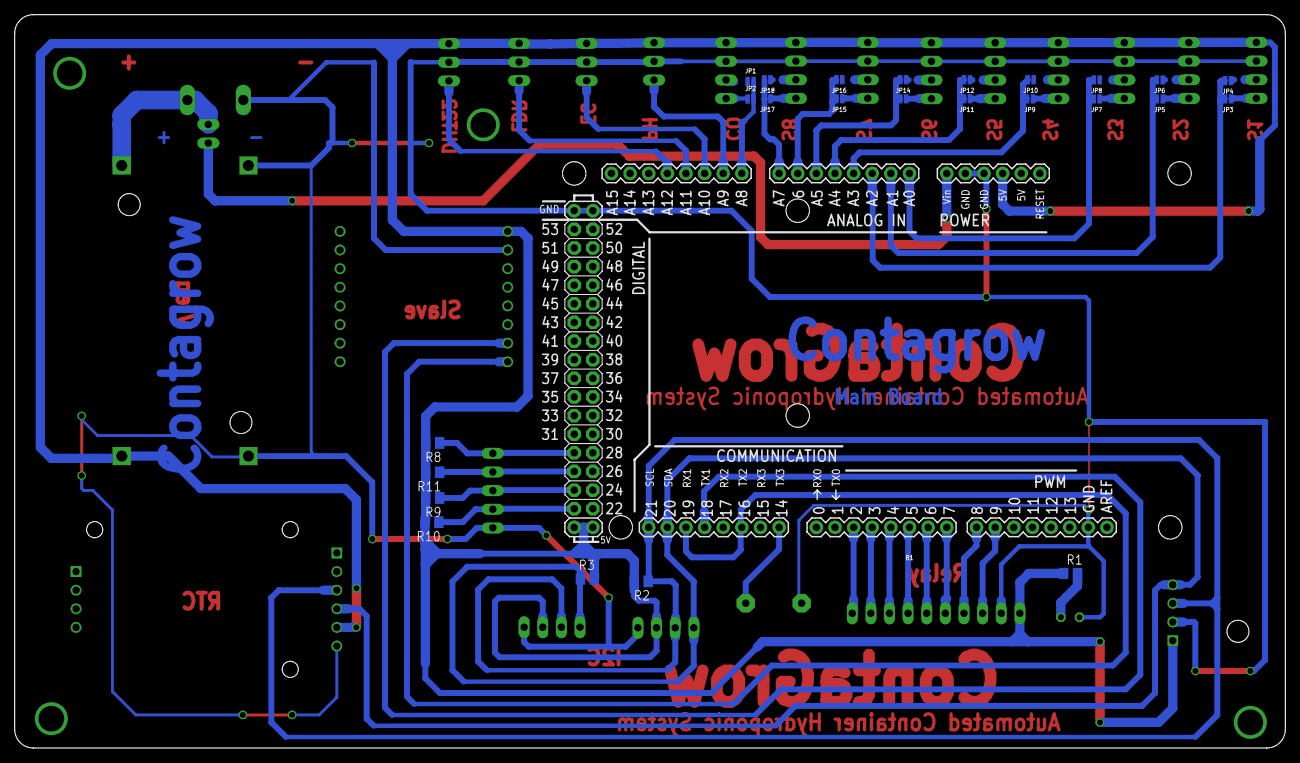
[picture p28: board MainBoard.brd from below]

Board: 2 copper layers, 173.3 x 100.0 mm, 51 parts (26 on the bottom side), 53 nets.

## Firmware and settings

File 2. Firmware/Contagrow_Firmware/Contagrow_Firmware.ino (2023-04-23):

#include "Pin.h"
#include <LiquidCrystal_I2C.h>
LiquidCrystal_I2C lcd(0x27, 20, 4); // set the LCD address to 0x27 for a 16 chars and 2 line display

//float sensor_volt;
//float RS_gas;
//float ratio;

const int rs = 12, rw = 1, en = 11, d4 = 5, d5 = 4, d6 = 3, d7 = 2;
int Menu, Up, Down, Ok;
int lockMenu = 0, lockUp = 0, lockDown = 0, lockOk = 0;
int dis, sub = 0, mode = 0;

void setup() {
  first_setup();
//  relayon();
}
void loop() {
  //  relayon();
  relayOn();
  //  bmeDebug();
  //  int soil1 = analogRead(SOIL1);  // Read the analog value form sensor
  //  Serial.println(soil1);
  //  buttonDebug();
  monitoring();

  //  airsensorDebug();

  //  Menu = digitalRead(23);
  //  Up =   digitalRead(27);
  //  Down = digitalRead(25);
  //  Ok =   digitalRead(29);
  //  tampil();


  //  dhtDebug();
  //  getCO();
}

void tampil()
{
  if (Menu == 0 && lockMenu == 0) {
    lockMenu = 1;
  } if (Menu != 0 && lockMenu == 1) {
    lockMenu = 0;
    dis = 1;
  }
  if (Menu == 0 && lockMenu == 0) {
    lockMenu = 1;
  } if (Menu != 0 && lockMenu == 1 && dis > 1) {
    lcd.clear();
    lockMenu = 0;
    dis = 1;
  }

  if (dis == 1)
  {

    // tampilan awal//
    lcd.setCursor(0, 0); lcd.print("|    Contagrow    |");
    lcd.setCursor(1, 1); lcd.print("Monitoring             ");
    lcd.setCursor(1, 2); lcd.print("Setting             ");
    lcd.setCursor(1, 3); lcd.print("None             ");

    if (Down == 0 && lockDown == 0) {
      lockDown = 1; //turunkan Cursor ">"
    }
    if (Down != 0 && lockDown == 1) {
      lcd.clear();
      lockDown = 0;
      mode++;
    }

    if (Up == 0 && lockUp == 0) {
      lockUp = 1; //naikkan Cursor ">"
    }
    if (Up != 0 && lockUp == 1) {
      lcd.clear();
      lockUp = 0;
      mode--;
    }
    switch (mode)
    {
      //      case 0 : lcd.setCursor(0, 0); lcd.print(">"); break;
      case 1 : lcd.setCursor(0, 1); lcd.print(">"); break;
      case 2 : lcd.setCursor(0, 2); lcd.print(">"); break;
      case 3 : lcd.setCursor(0, 3); lcd.print(">"); break;
    }
    if (Ok == 0 && lockOk == 0) {
      lockOk = 1;
      mode = 0;
    }
    //    if (Ok != 0 && lockOk == 1 && mode == 0) {
    //      lockOk = 0;  // pilih menu 1
    //      dis = 2;
    //      lcd.clear();
    //    }
    if (Ok != 0 && lockOk == 1 && mode == 1) {
      lockOk = 0;  // pilih menu 2
      dis = 3;
      lcd.clear();
    }
    if (Ok != 0 && lockOk == 1 && mode == 2) {
      lockOk = 0;  // pilih menu 3
      dis = 4;
      lcd.clear();
    }
    if (Ok != 0 && lockOk == 1 && mode == 3) {
      lockOk = 0;  // pilih menu 4
      dis = 5;
      lcd.clear();
    }

    if (mode > 3 || mode < 0) mode = 0;

  }
  if (dis == 2)
  {
    if (sub == 0)
    {
      //      lcd.setCursor(0, 0); lcd.print("Monitoring             ");
      //      lcd.setCursor(1, 1); lcd.print("Sub Menu 1        ");
      //      lcd.setCursor(1, 2); lcd.print("Sub Menu 2        ");
      //      lcd.setCursor(1, 3); lcd.print("Sub Menu 3        ");
      monitoring();
      if (Down == 0 && lockDown == 0) {
        lockDown = 1; //turunkan Cursor ">"
      }
      if (Down != 0 && lockDown == 1) {
        lcd.clear();
        lockDown = 0;
        mode++;
      }

      if (Up == 0 && lockUp == 0) {
        lockUp = 1; //naikkan Cursor ">"
      }
      if (Up != 0 && lockUp == 1) {
        lcd.clear();
        lockUp = 0;
        mode--;
      }
      if (Ok != 0 && lockOk == 1 && mode == 0) {
        lockOk = 0;  // Isi submenu 1
        lcd.clear();
        sub = 1;
      }
      if (Ok != 0 && lockOk == 1 && mode == 1) {
        lockOk = 0;  // Isi submenu 2
        lcd.clear();
        sub = 2;
      }
      if (Ok != 0 && lockOk == 1 && mode == 2) {
        lockOk = 0;  // Isi submenu 3
        lcd.clear();
        sub = 3;
      }

      if (mode > 2 || mode < 0) mode = 0;
      {
        switch (mode)
        {

          case 1 : lcd.setCursor(0, 2); lcd.print(">"); break;
          case 2 : lcd.setCursor(0, 3); lcd.print(">"); break;
        }
      }
    }
  }

  if (dis == 3)
  { //menu kontrol manual
    lcd.setCursor(0, 0); lcd.print("Manual Control  ");
    lcd.setCursor(1, 1); lcd.print("Relay 1:        ");
    lcd.setCursor(1, 2); lcd.print("Relay 2:        ");
    lcd.setCursor(1, 3); lcd.print("Relay 3:        ");
  }

  if (dis == 4)
  {
    lcd.setCursor(0, 0); lcd.print("Menu 3             ");
    lcd.setCursor(1, 1); lcd.print("Sub Menu 1        ");
    lcd.setCursor(1, 2); lcd.print("Sub Menu 2        ");
    lcd.setCursor(1, 3); lcd.print("Sub Menu 3        ");
  }

  if (dis == 5)
  {
    lcd.setCursor(0, 0); lcd.print("Menu 4             ");
    lcd.setCursor(1, 1); lcd.print("Sub Menu 1        ");
    lcd.setCursor(1, 2); lcd.print("Sub Menu 2        ");
    lcd.setCursor(1, 3); lcd.print("Sub Menu 3        ");
  }
  //isi menu1////
  if (dis == 2 && sub == 1) {
    lcd.setCursor(0, 1);
    lcd.print(" Isi Sub Menu 1:::");
  }
  if (dis == 2 && sub == 2) {
    lcd.setCursor(0, 1);
    lcd.print(" Isi Sub Menu 2::");
  }
  if (dis == 2 && sub == 3) {
    lcd.setCursor(0, 1);
    lcd.print(" Isi Sub Menu 3:");
  }
}

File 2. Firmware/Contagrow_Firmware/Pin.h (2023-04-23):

#define     COPIN           A8 //kanan
#define     DHTPIN          A9
#define     PHSensor        A12 //kanan
#define     ECSensor        A10


#define     SOIL1           A2//kanan
#define     SOIL2           A1
#define     SOIL3           A0 //kanan
#define     SOIL4           A3
#define     SOIL5           A4 //kanan
#define     SOIL6           A5
#define     SOIL7           A6 //kanan
#define     SOIL8           A7

#define     Relay1          2//kanan
#define     Relay2          3
#define     Relay3          4 //kanan
#define     Relay4          5
#define     Relay5          6 //kanan
#define     Relay6          7
#define     Relay7          8
#define     Relay8          9

#define     button1         29 //Paling kanan
#define     button2         27
#define     button3         25
#define     button4         23 //Paling Kiri

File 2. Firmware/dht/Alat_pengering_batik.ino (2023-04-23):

#include <OneWire.h>
#include <DallasTemperature.h>
#include "DHT.h"
#include <Wire.h>
#include <LiquidCrystal_I2C.h>
#include <Servo.h>
#include <virtuabotixRTC.h>

#define DHTPIN1 3
#define DHTPIN2 4
#define DHTTYPE DHT22
#define ONE_WIRE_BUS 2
#define TEMPERATURE_PRECISION 9
#define button1 8
#define button2 9
#define button3 10
#define button4 11
#define pompa 14
#define radiator 15
#define resetdht 5
#define blower 16
#define bounce 10



LiquidCrystal_I2C lcd(0x20, 128, 64);
LiquidCrystal_I2C lcd2(0x26 , 20, 4);
DHT dht1 (DHTPIN1, DHTTYPE);
DHT dht2 (DHTPIN2, DHTTYPE);
OneWire oneWire(ONE_WIRE_BUS);
DallasTemperature suhu(&oneWire);
Servo servoinlet, servooutlet;
virtuabotixRTC myRTC(22, 23, 24);//urut

float tempc, t1, t2, h1, h2, rata2t, rata2h;
float tempair;
int varair = 40,  varvent = 90, varruang = 55;
int jam, menit, kondisi = 0, servo = 0, timer = 0, truang = 0;
int jammon, menmon, detmon = 0, timemon = 0;
int jamstat = 0, menstat = 2;
String notif = "[START]", notif1 = "Sistem Mati";


void setup() {
  Serial.begin(115200);
  pinMode(1, HIGH);
  suhu.begin();
  dht1.begin();
  dht2.begin();
  lcd.begin();
  lcd2.begin();
  servoinlet.attach(7);
  servooutlet.attach(6);
  lcd.backlight();
  lcd2.backlight();
  // seconds, minutes, hours, day of the week, day of the month, month, year
  //    myRTC.setDS1302Time(00, 5, 14, 6, 29, 7, 2021);

  pinMode(button1, INPUT_PULLUP);
  pinMode(button2, INPUT_PULLUP);
  pinMode(button3, INPUT_PULLUP);
  pinMode(button4, INPUT_PULLUP);
  pinMode(pompa, OUTPUT);
  pinMode(radiator, OUTPUT);
  pinMode(resetdht, OUTPUT);
  pinMode(blower, OUTPUT);
  digitalWrite(pompa, HIGH);
  digitalWrite(radiator, HIGH);
  digitalWrite(blower, HIGH);
  servoinlet.write(0);
  delay(1000);
  servooutlet.write(1);
  delay(500);
  servooutlet.write(0);
  delay(500);
  servoinlet.detach();
  servooutlet.detach();

}


void loop() {


  lcd.clear();
  lcd2.clear();
  lcd.setCursor(0, 0);
  lcd.print("Alat Pengering Batik");
  lcd.setCursor(4, 1);
  lcd.print("PKM-PI 2021");
  lcd.setCursor(8, 2);
  lcd.print("UGM");
  lcd.setCursor(0, 3);
  lcd.print(notif);
  lcd.setCursor(11, 3);
  lcd.print("[Setting]");


  //LCD Monitor
  lcd2.setCursor(0, 0);
  lcd2.print("Suhu Air    =");
  lcd2.print(tempc);
  lcd2.print((char)223);
  lcd2.print("C");
  lcd2.setCursor(0, 1);
  lcd2.print("Suhu Ruangan=");
  lcd2.print(rata2t);
  lcd2.print((char)223);
  lcd2.print("C");
  lcd2.setCursor(0, 2);
  lcd2.print("Kelembaban  =");
  lcd2.print(rata2h);
  lcd2.print(" %");
  
  lcd2.setCursor(4, 3);
  lcd2.print(notif1);

  semua();
  suhu_air();
  myRTC.updateTime();
  dht();

  if (digitalRead(button4) == LOW) {
    delay (bounce);
    while (digitalRead(button4) == LOW) {}
    Serial.print("button dipencet");
    lcd.clear();
    menusetting();
  }

  if (digitalRead(button2) == LOW) {
    delay (bounce);
    while (digitalRead(button2) == LOW) {}
    digitalWrite(1, LOW);
    delay(1000);
    digitalWrite(1, HIGH);
    delay(1000);
  }

  if (digitalRead(button1) == LOW) {
    delay (bounce);
    while (digitalRead(button1) == LOW) {}
    mulai();
    lcd.clear();
    lcd.setCursor(4, 1);
    lcd.print("Please Wait..");
  }

  if (tempc > varair+2 and kondisi == 1)  {
    notif1 = "Sistem Hidup";
    notif = "[RUN]";
    digitalWrite(pompa, LOW);
    digitalWrite(radiator, LOW);

    if (timer == 1) {
      menit = myRTC.minutes + menit;
      jam = myRTC.hours + jam;
      timer = 0;
      timemon = 1;
    }
    if (jam == myRTC.hours and menit == myRTC.minutes) {
      jam = 0;
      menit = 0;
      kondisi = 0;
    }
    else if (rata2h > varvent) {

      if (servo == 0) {

        exhaust_nyala();
        servo = 1;
        Serial.print("exhaust nyala");
      }
    }


    else if (rata2h < varvent - 2) {

      if (servo == 1) {
        exhaust_mati();
        servo = 0;
        Serial.print("exhaust mati");
      }

    }
    if (rata2t > varruang and truang == 0) {
      kondisi = 0;
      truang = 1;
      if (servo == 1) {
        exhaust_mati();
        servo = 0;

      }
    }

  }

  if (rata2t < (varruang - 5) and tempc > varair and truang == 1) {
    kondisi = 1;
    truang = 0;
  }

  if (tempc < varair or kondisi == 0  ) {
    digitalWrite(pompa, HIGH);
    digitalWrite(radiator, HIGH);
    if (servo == 1) {
      exhaust_mati();
      servo = 0;
    }
    Serial.print("sistem mati");
    notif = "[START]";
    notif1 = "Sistem Mati";
  }
  if (isnan(h1) or isnan(t1) or isnan(h2) or isnan(t2)) {
    digitalWrite(resetdht, LOW);
    delay(2000);
    digitalWrite(resetdht, HIGH);
    Serial.println("RESET!!!!!!!");
  }

  Serial.print(myRTC.hours);
  Serial.print(":");
  Serial.print(myRTC.minutes);
  Serial.print(":");
  Serial.println(myRTC.seconds);



  delay(1000);
}

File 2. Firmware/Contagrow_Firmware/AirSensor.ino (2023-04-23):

const int DO = 8;
#include <Wire.h>
#include <Adafruit_Sensor.h>
#include <Adafruit_BME280.h>
#define SEALEVELPRESSURE_HPA (1013.25)
Adafruit_BME280 bme;
float bmeTemp, bmeHumid, bmePressure, bmeAltitude;
float sensor_volt;
float RS_gas;
float ratio;
int sensorValue;
float R0 = 0.10;

void getairSensor()
{
  getDht();
  getBme();
  getCO();
}

void getCO()
{
  sensorValue = analogRead(COPIN);
  sensor_volt = ((float)sensorValue / 1024) * 5.0;
  RS_gas = (5.0 - sensor_volt) / sensor_volt; // Depend on RL on yor module
  ratio = RS_gas / R0; // ratio = RS/R0
  //------------------------------------------------------------/
  //  Serial.print("sensor_volt = ");
  //  Serial.println(sensor_volt);
  //  Serial.print("RS_ratio = ");
  //  Serial.println(RS_gas);
  //  Serial.print("Rs/R0 = ");
  //  Serial.println(ratio);
  //  Serial.print("\n\n");
  //  delay(10);
}


//=============================================================================== DHT 22 ======================================================================
#include <DHT.h>;
#define DHTTYPE DHT22   // DHT 22  (AM2302)
DHT dht(DHTPIN, DHTTYPE); //// Initialize DHT sensor for normal 16mhz Arduino
float dhtHumidity;  //Stores humidity value
float dhtTemperature; //Stores temperature value

void getDht()
{
  dhtHumidity = dht.readHumidity();
  dhtTemperature = dht.readTemperature();
  //  Serial.print("Humidity: ");
  //  Serial.print(dhtHumidity);
  //  Serial.print(" %, Temp: ");
  //  Serial.print(dhtTemperature);
  //  Serial.println(" Celsius");
}

void dhtDebug()
{
  getDht();
  Serial.print("Humidity: ");
  Serial.print(dhtHumidity);
  Serial.print(" %, Temp: ");
  Serial.print(dhtTemperature);
  Serial.println(" Celsius");
}




//=============================================================================== BME ======================================================================
void getBme()
{
  bmeTemp = bme.readTemperature();
  bmeHumid = bme.readHumidity();
  bmePressure = bme.readPressure() / 100.0F;
  bmeAltitude = bme.readAltitude(SEALEVELPRESSURE_HPA);
  //  Serial.print("Temperature = ");
  //  Serial.print(bmeTemp);
  //  Serial.println("*C");
  //
  //  Serial.print("Pressure = ");
  //  Serial.print(bmeHumid);
  //  Serial.println("hPa");
  //  delay(500);
}

void bmeDebug()
{
  getBme();
  Serial.print("Temperature = ");
  Serial.print(bmeTemp);
  Serial.println("*C");

  Serial.print("Pressure = ");
  Serial.print(bmeHumid);
  Serial.println("hPa");

  Serial.print("Approx. Altitude = ");
  Serial.print(bmePressure);
  Serial.println("m");

  Serial.print("Humidity = ");
  Serial.print(bmeAltitude);
  Serial.println("%");
  Serial.println();
  //  delay(1000);
}
unsigned long lastTime;

void airsensorDebug() //sampling every 10 second
{

  //  if (millis() - lastTime > 10000)
  //  {
  //    getairSensor();
  //    Serial.print(bmeTemp); Serial.print("\t");
  //    Serial.print(bmeHumid); Serial.print("\t");
  //    Serial.print(dhtTemperature); Serial.print("\t");
  //    Serial.print(dhtHumidity); Serial.print("\t");
  //    Serial.print(ratio); Serial.println("\t");
  //    lastTime = millis(); //Update the timer
  //  }
  //  else
  //  {
  //    Serial.print(bmeTemp); Serial.print("\t");
  //    Serial.print(bmeHumid); Serial.print("\t");
  //    Serial.print(dhtTemperature); Serial.print("\t");
  //    Serial.print(dhtHumidity); Serial.print("\t");
  //    Serial.print(ratio); Serial.println("\t");
  //  }

  //  getairSensor();
  //  Serial.print(bmeTemp); Serial.print("\t");
  //  Serial.print(bmeHumid); Serial.print("\t");
  //  Serial.print(dhtTemperature); Serial.print("\t");
  //  Serial.print(dhtHumidity); Serial.print("\t");
  //  Serial.print(ratio); Serial.println("\t");

  const unsigned long fiveMinutes = 1 * 60 * 1000UL;
  static unsigned long lastSampleTime = 0 - fiveMinutes;  // initialize such that a reading is due the first time through loop()

  unsigned long now = millis();
  if (now - lastSampleTime >= fiveMinutes)
  {
    lastSampleTime += fiveMinutes;
    getairSensor();
    Serial.print(bmeTemp); Serial.print("\t");
    Serial.print(bmeHumid); Serial.print("\t");
    Serial.print(dhtTemperature); Serial.print("\t");
    Serial.print(dhtHumidity); Serial.print("\t");
    Serial.print(ratio); Serial.println("\t");
  }
}

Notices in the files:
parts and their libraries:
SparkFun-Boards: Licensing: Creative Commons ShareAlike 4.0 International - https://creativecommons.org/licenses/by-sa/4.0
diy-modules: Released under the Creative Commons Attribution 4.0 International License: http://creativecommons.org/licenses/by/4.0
